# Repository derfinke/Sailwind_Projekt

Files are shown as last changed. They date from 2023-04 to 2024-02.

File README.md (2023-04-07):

# Projektarbeit: Sailwind Steuerung
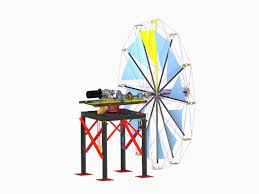
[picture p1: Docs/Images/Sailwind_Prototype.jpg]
Product Name Screen Shot
 \
Firmware/Schaltplan für die Steuerung des Sailwind 4.0 Projekts.\
[ Für weitere Informationen](https://www.sailwind-power.eu/)

## Geteilte Dokumente
[Bauteile Tabelle](https://drive.google.com/drive/folders/1qaNF0T8h1C8PEslQvWO4vngNG08Ppogr?usp=share_link)

## Roadmap
- [x] Erstellung des Schaltplans
- [ ] Erstellung des PCB Designs
	- [x] Auswahl der Bauteile
- [ ] Erstellung der Firmware
	- [x] Definieren der genutzen Ports
	- [ ] Definition des Ethernet Protokoll
	- [ ] Siehe [open issues](https://github.com/derfinke/Sailwind_Projekt/issues)

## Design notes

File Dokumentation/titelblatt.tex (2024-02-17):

\begin{titlepage}
\vspace*{-3cm}
    \begin{figure}[ht]
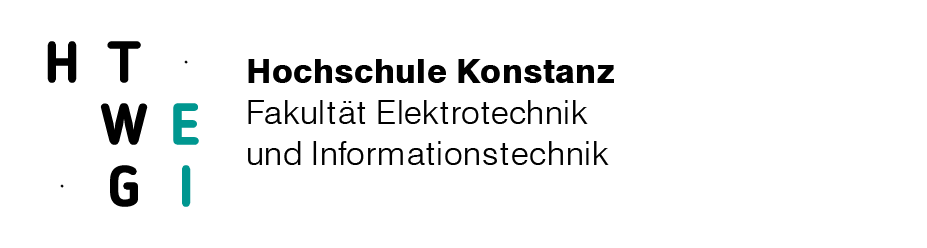
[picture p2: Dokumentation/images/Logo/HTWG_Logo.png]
        \hspace{7cm}\subfloat{{ }}
    \end{figure}
        
	\begin{center}
		\vspace*{1cm}
		\LARGE\bf\myTopic\\
		\vspace*{1cm}
		\normalsize\rm
		\vspace*{1cm}
		\textbf{Projektarbeit}\\
		\vspace*{0.5cm}
		An der Fakultät Elektro- und Informationstechnik \\
		\vspace*{0.5cm}
		vorgelegt von  \\
	    \vspace*{0.25cm}
		\textbf{\myAutorTwo\:und \myAutor}  \\
		\vspace*{0.25cm}
		Matrikelnummer: \myMatrikelnummerTwo\:und \myMatrikelnummer \\
		\vspace*{1cm}
		Hochschule Konstanz für Technik, Wirtschaft und Gestaltung \\
		\vspace*{1cm}
		Hochschulbetreuer: \\
		\textbf{\mySupervisorTwo}\\
		\textbf{\mySupervisor}\\
		\vspace*{1cm}
		\textbf{Konstanz den \today}
	\end{center}
\end{titlepage}
\newpage
\setcounter{page}{2}

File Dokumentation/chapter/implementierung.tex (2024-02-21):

\section{Software}
Die Steuerung der Segel soll durch zwei verteilte Systeme erfolgen, die über eine Ethernet-Verbindung miteinander kommunizieren. Die Idee dahinter ist, die Berechnungen für die Ausrichtung der Segel in Abhängigkeit der Windstärke und -Richtung (Controllino) von der hardwarenahen Verarbeitung der Sensoren und Aktuatoren (STM32) logisch zu trennen. \\

\noindent
Die vorliegende Arbeit konzentriert sich dabei lediglich auf das System der Sensoren und Aktuatoren, welches mit dem STM32 realisiert wurde. Die Aufgabe dieses Systems ist, zunächst die Linearführung zu kalibrieren, damit die aktuelle Position korrekt ermittelt werden kann. Außerdem soll über die Buttons am Gehäuse und zusätzlich über einen Webserver eine manuelle Steuerung ermöglicht werden. Während des Automatikbetriebs geschieht ein regelmäßiger Austausch aller relevanter Daten über eine REST basierte Schnittstelle. Dies beinhaltet u.A. die Information über aktuelle Windbedingung, Position der Segel, eventuelle Fehlerzustände (z.B. Motorfehler oder Überstrom) und daraus resultierende Befehle zur Anpassung der Segelstellung.
Für die Implementierung wurde die Software in komponentenorientierte Module eingeteilt:
\begin{figure}[H]
	\centering
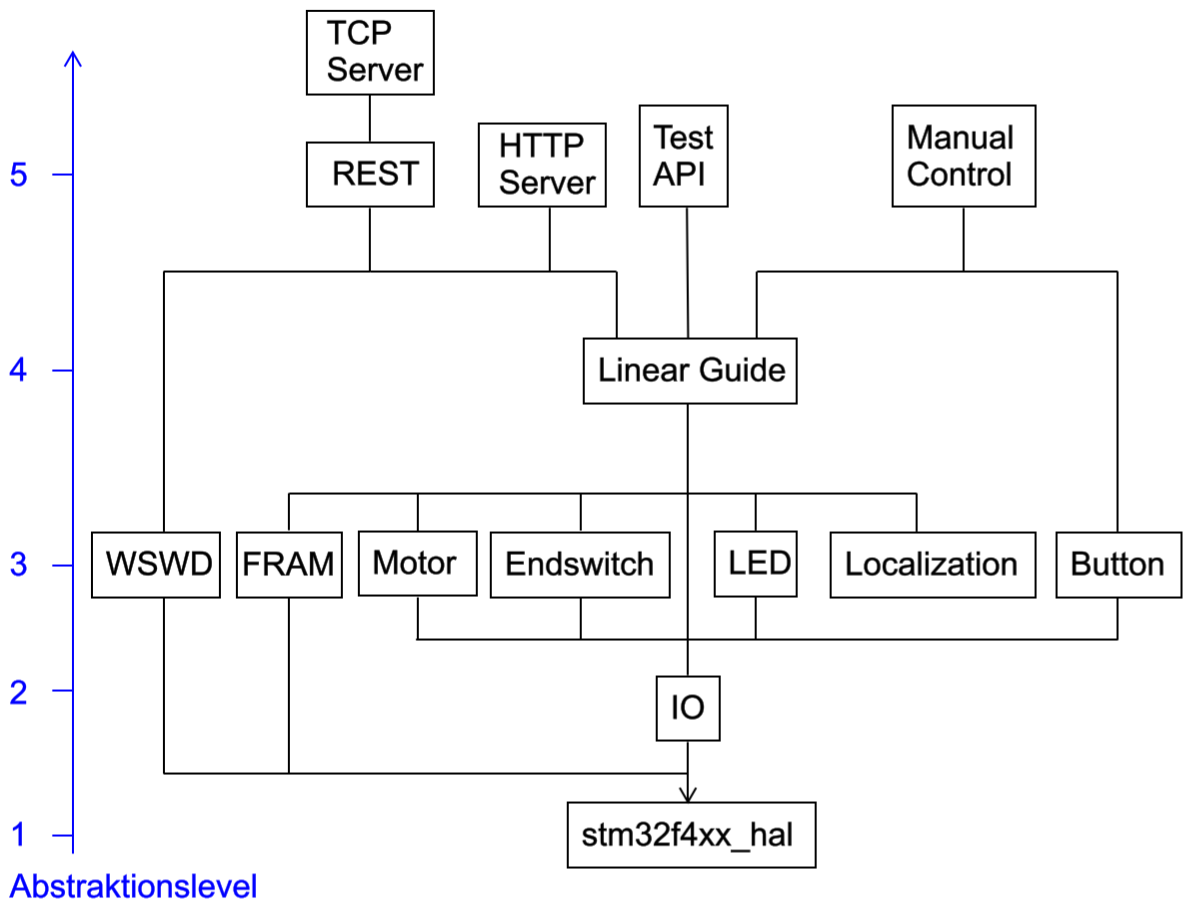
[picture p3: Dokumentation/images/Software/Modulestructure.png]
	
	\caption{Software Modulstruktur}
	\label{fig:modulestructure}
\end{figure}
\noindent
\autoref{fig:modulestructure} zeigt abwärtsgerichtet, wie die einzelnen Module aufeinander zugreifen. Auf unterster Abstraktionsebene laufen jegliche Operationen über die Standardbibliothek des Mikrocontrollers \verb|stm32f4xx\_hal|. Darüber liefert das \verb|IO|-Modul ein Set aus Hilfsfunktionen und -Strukturen für den allgemeinen Zugriff auf die \ac{GPIO}-Pins und zum Auslesen analoger Messwerte der einzelnen Sensoren.\\

\noindent
Ebene drei umfasst hauptsächlich Module, welche alle relevanten Funktionalitäten der physischen Teilkomponenten des Systems implementieren, wie z.B. das Anemometer \verb|WSWD| oder der \verb|Motor|. Einige davon greifen dabei auf das \verb|IO|-Modul zu, wobei der allgemeine GPIO-Zugriff von einer spezifischen Funktion eingekapselt wird, wie z.B. das Einschalten einer LED im Falle des \verb|LED|-Moduls. Eine Ausnahme ist das \verb|Localization|-Modul, welches keine physische Komponente darstellt, sondern einige Hilfsfunktionen zur Kalibrierung und Positionsberechnung bereitstellt.\\

\noindent
Während die Module bis Ebene drei überwiegend allgemeingültig entworfen sind, enthält das \verb|Linear Guide|-Modul anwendungsspezifische Funktionen. Als zentrales Element bildet dieses ein High-Level Interface zur Verwendung der Teilkomponenten \verb|FRAM|, \verb|Motor|, \verb|Endswitch|, \verb|LED|, \verb|Localization| und \verb|IO|. \\

\noindent
Die Module der obersten Abstraktionsebene bilden die direkten Schnittstellen zur Außenwelt. Das \verb|Manual Control|-Modul ermöglicht die manuelle Steuerung der Linearführung über die User-Buttons am Gehäuse und insbesondere die Umsetzung des Kalibrierungsprozesses. Auf der anderen Seite kann das System auch durch einen \ac{HTTP} Webserver überwacht und gesteuert werden. Außerdem werden im \verb|REST|-Modul die Anfragen des Controllinos über die \verb|TCP Server|-Verbindung verarbeitet, wie bereits oben erwähnt. Zuletzt wurde ein \verb|Test|-Modul implementiert, dass die Funktionalitäten der Module auf Ebene drei verifiziert. Dazu wurde ein einfaches Batch-Skript geschrieben, das die einzelnen Testcases auflistet und die Auswahl über UART an den  Mikrocontroller sendet, sodass im \verb|Test|-Modul eine entsprechende Funktion ausgeführt wird. In den nachfolgenden Abschnitten wird genauer auf einige Module eingegangen, beginnend mit dem untersten Abstraktionslevel.

\subsection{IO-Modul}
Dieses Modul soll den lesenden und schreibenden Zugriff auf jegliche GPIO-Pins erleichtern, die zur Kontrolle jeglicher Steuerelemente angeschlossen wurden. Allgemein besteht das System aus analogen und digitalen Sensoren bzw. Aktuatoren. Für jede Form wurde eine repräsentative Struktur definiert, in der alle relevanten Daten zusammengefasst werden.
\subsubsection{Digitale Pins}
Für digitale Ein- und Ausgänge wurde eine gemeinsame Struktur \verb|IO_digitalPin_t| definiert:
\begin{lstlisting}[language=C, caption={Struktur für digitale Pins}, label={lst:digitalPin}]
typedef struct {
	GPIO_TypeDef *GPIOx;
	uint16_t GPIO_Pin;
	GPIO_PinState state;
} IO_digitalPin_t;
\end{lstlisting}
Dabei ist der GPIO-Pin durch eine Nummer \verb|GPIO_Pin| und einen Port \verb|GPIOx| definiert. Zusätzlich wird in der Struktur der aktuelle Zustand \verb|state| (null oder eins) gespeichert. Diese kann nun einer Funktion als Pointer übergeben werden, um z.B. den neuen Zustand auszulesen:
\begin{lstlisting}[language=C, caption={Einlesen eines digitalen Pin-Zustands}, label={lst:digitalRead}]
GPIO_PinState IO_digitalRead(IO_digitalPin_t *dig_IN) {
	dig_IN->state = HAL_GPIO_ReadPin(
		dig_IN->GPIOx, dig_IN->GPIO_Pin
	);
	return dig_IN->state;
}
\end{lstlisting}
Dabei wird lediglich die Funktion \verb|HAL_GPIO_ReadPin()| der \verb|stm32f4xx_hal| Bibliothek aus \autoref{fig:modulestructure} aufgerufen, welche die zuvor besagten Attribute des Pins entgegennimmt und dessen Wert zurückgibt. Das Speichern dieses Werts in \verb|state| hat den Vorteil, dass damit auf eine Änderung des Zustandes geschlossen werden kann. Dies ist z.B. für das Erfassen der steigenden und fallenden Flanke während eines Knopfdrucks sinnvoll und wurde wie folgt realisiert:
\begin{lstlisting}[language=C, caption={Detektion einer Flanke}, label={lst:edgeDetection}]
boolean_t IO_digitalRead_state_changed(IO_digitalPin_t *dig_IN) {
	GPIO_PinState previous_state = dig_IN->state;
	GPIO_PinState current_state = IO_digitalRead(dig_IN);
	return current_state ^ previous_state;
}
\end{lstlisting}
Die Funktion in \autoref{lst:edgeDetection} gibt durch eine logische exklusiv-oder-Verknüpfung von letztem und aktuellem Zustand in Form eines booleschen Werts an, ob sich der Zustand geändert hat oder nicht. Äquivalent zu \autoref{lst:digitalRead} ist eine Funktion \verb|IO_digital_write()| implementiert, die den gewünschten Pegel an einem entsprechenden Ausgangspin schaltet.
\subsubsection{Analoge Pins}
Etwas komplexer wird es mit dem Auslesen von analogen Sensorwerten. Dazu wird ein ADC-Kanal (\verb|ACD_Channel|) des STM32 verwendet, der eine Spannung am Pin zwischen 0 und 3.3V in eine 12 bit Sequenz quantisiert und folglich als Integerwert \verb|ADC_val| zwischen 0 und 4096-1 zurückgibt. Idealerweise entspricht dieser Wertebereich umgewandelt dem des Sensors, jedoch ist dies durch Ungenauigkeiten in der Hardware nicht immer der Fall, weshalb dies durch zusätzliche Grenzwerte in der Struktur für analoge Sensoren berücksichtigt wird:
\begin{lstlisting}[language=C, caption={Struktur für analoge Sensoren}, label={lst:analogSensor}]
typedef struct {
	ADC_HandleTypeDef *hadc_ptr;
	IO_SensorType_t Sensor_type;
	uint32_t ADC_Channel;
	uint16_t ADC_val;
	uint16_t max_sens_val;
	uint16_t sens_val;
	uint16_t min_sens_val;
	float max_pin_volt;
	float min_pin_volt;
} IO_analogSensor_t;
\end{lstlisting}
Die Bezeichnung \verb|sense_val| aus \autoref{lst:analogSensor} steht dabei für den Wert in der Einheit des gewünschten Sensormesswerts und \verb|pin_volt| für den umgewandelten Spannungswert am Pin. Damit lässt sich der Sensormesswert wie folgt berechnen:\footnote{Funktion dient zur Veranschaulichung und wurde nicht exakt in dieser Form implementiert}
\begin{lstlisting}[language=C, caption={Konvertierung des rohen Analogwerts}, label={analogRead}]
void IO_Convert_from_ADC(IO_analogSensor_t *s) {
	float pin_volt = 3.3 * s->ADC_val / (4096-1)
	s->sens_val = (s->max_sens_val - s->min_sens_val) /
	              (s->max_pin_volt - s->min_pin_volt) *
	              (pin_volt        - s->min_pin_volt) +
	               s->min_sens_val
}
\end{lstlisting}
In umgekehrter Weise funktioniert die Umwandlung eines gewünschten Wertes in einen quantisierten Spannungswert für einen analogen Aktuator mithilfe einer entsprechenden Struktur \verb|IO_analogActuator_t|. \\

\noindent
Die Module \verb|LED|, \verb|Button| und \verb|Endswitch|, repräsentieren physische Komponenten, die jeweils durch einen einfachen digitalen Pin angesteuert werden und enthalten daher lediglich Wiederverwendungen der Funktionen \verb|IO_digitalWrite()|, um eine LED ein und auszuschalten, \verb|IO_digitalRead_state_changed()|, um einen Knopfdruck zu erfassen oder \verb|IO_digitalRead()|, um den Zustand eines Endschalters zu lesen. Dagegen wird der BG 45x30 SI Gleichstrommotor aufgrund seiner internen Regelung durch mehrere verschiedene Ein- und Ausgänge angesteuert.
\subsection{Motor-Modul}
Die Aufgabe des Motors ist, die Segelstellung entlang der Linearführung anzupassen. Dazu ermöglichen dessen digitale Eingänge gemäß \autoref{tab:digitale_Eingaenge} eine flexible Einstellung der Drehzahl und -Richtung. Alternativ zu den konfigurierbaren fixen Geschwindigkeiten 1 und 2 kann mit dem analogen Eingang auch eine beliebige Drehzahl dynamisch vorgeben werden. Damit konnte eine Drehzahlrampe realisiert werden, die einen sanfteren Brems- und Beschleunigungsvorgang gewährleistet.\\

\noindent
Über die digitalen Ausgänge kann der Ist-Zustand überwacht werden, darunter die aktuelle Drehrichtung und ob ein Fehler vorliegt. Zusätzlich kann durch ein Puls-Signal mit 12 Pulsen pro Umdrehung auf die Drehzahl geschlossen werden. Da der Motor in diesem Fall jedoch unter Drehzahlregelung betrieben wird, kann, sofern kein Fehlersignal vorliegt, von einer ausreichend präzisen Einhaltung der eingestellten Drehzahl ausgegangen werden. Dennoch ist das Puls-Signal von zentraler Bedeutung, da aufgrund der Gewindesteigung der Linearführung und der Anzahl der Pulse ausgehend von einem Endpunkt die aktuelle Position und somit die Segelstellung ermittelt werden kann. Das Zählen der Pulse geschieht jedoch der Thematik entsprechend in einer Funktion des \verb|Localization|-Moduls, die durch einen externen Interrupt am zuständigen GPIO-Pin von steigenden Flanken getriggert wird.\\

\noindent
Orientiert an der Architektur des \verb|IO|-Moduls dient auch hier eine Struktur als gemeinsamer Zugriffspunkt aller relevanter Daten des Motors:
\begin{lstlisting}[language=C, caption={Struktur des Motors}, label={lst:motor}]
typedef struct {
	Motor_function_t current_function;
	Motor_INs_t INs;
	IO_analogActuator_t AIN_set_rpm;
	IO_digitalPin_t OUT2_error;
	IO_digitalPin_t OUT3_rot_dir;
	uint16_t normal_rpm;
	uint16_t rpm_set_point;
	uint16_t ramp_final_rpm;
	uint32_t ramp_last_step_ms;
	boolean_t ramp_activated;
} Motor_t;
\end{lstlisting}
\subsubsection{Funktionsvorgabe}
Grundlage zur Steuerung des Motors ist die Implementation der Funktionsvorgabe über die digitalen Eingänge, die in der Struktur nach \autoref{lst:motor} durch ein Array \verb|INs| des Typs \verb|IO_digitalPin_t| organisiert sind. Zur einfachen Anwendung wurde ein enum \verb|Motor_function_t| definiert, der alle Funktionen entsprechend \autoref{tab:digitale_Eingaenge} bezeichnet und von oben beginnend von null bis sieben nummeriert. Durch eine geeignete Umrechnung in einen Binärwert zwischen 00 und 11 können aus den einzelnen Stellen direkt die passenden beiden Pins über das Array indiziert und mit den Stellenwerten beschrieben werden. Das nachfolgende Listing zeigt die genaue Umsetzung dieses Verfahrens.
\begin{lstlisting}[language=C, caption={Einstellung der Motorfunktionen}, label={lst:motorFunction}]
void Motor_set_function(Motor_t *motor, Motor_function_t func) {
	motor->current_function = func;
	uint8_t pin_offset = (func >= 4) * 2;
	int8_t function_bits = func - pin_offset * 2;
	for (int i = 0; i < 2; i++) {
		GPIO_PinState state = function_bits & 2 ? 1 : 0;
		uint8_t IN_idx = i + pin_offset;
		IO_digitalWrite(&motor->INs[IN_idx], state);
		function_bits <<= 1;
	}
}
\end{lstlisting}
Im ersten Schritt wird überprüft, ob die Eingänge 0 \& 1 oder 2 \& 3 für die Funktion zuständig ist. Letzteres ist der Fall, wenn der Funktionsindex in der oberen Hälfte (\verb|>=4|) liegt. Das Beschreiben der beiden Eingänge erfolgt iterativ über eine For-Schleife, wobei die Pins durch die Zählvariable \verb|i| indiziert werden. Falls die Eingänge 2 \& 3 zuständig sind, muss folglich ein \verb|pin_offset| von zwei auf den Index addiert werden. Ebenfalls wird dann die Funktionsnummer mit vier subtrahiert, damit aus dem resultierenden Wert in \verb|function_bits| der zweistellige Binärwert errechnet werden kann.
Durch die bitweise und-Verknüpfung mit zwei und einer anschließenden einfachen links-shift Operation (\acs{MSB}-first) werden die einzelnen Binärstellen der Reihe nach berechnet und mit \verb|IO_digitalWrite()| als neuen Zustand \verb|state| am passenden Pin geschaltet.
\subsubsection{Drehzahlrampe}
Darauf basierend wurden konkrete Funktionen zur Steuerung des Motors implementiert. Das Kernelement ist dabei die Realisierung der Drehzahlrampe innerhalb der Funktion \verb|Motor_speed_ramp()|, welche in der Hauptschleife des Programms durchgehend ausgeführt wird. Die Rampe kann dabei durch eine Funktion \verb|Motor_start_moving()| aktiviert werden, die mit \verb|Motor_set_function()| Links- oder Rechtslauf einstellt und anschließend das Flag \verb|ramp_activated| aus \autoref{lst:motor} setzt. Darauf hin wird der Drehzahlwert \verb|rpm_setpoint| in regelmäßigen Zeitschritten um einen konstanten Wert erhöht. Nach Konfiguration auf \textit{Drehzahlvorgabe} (\autoref{tab:digitale_Eingaenge}) kann die neue Soll-Drehzahl an dem analogen Eingang \verb|AIN_set_rpm| mit \verb|IO_analogWrite()| umgesetzt werden. Dies geschieht solange, bis die Zieldrehzahl \verb|ramp_final_rpm=normal_rpm| erreicht ist und die Rampe wieder deaktiviert wird. Ebenso kann die Rampe mit \verb|Motor_stop_moving()| für den Bremsvorgang aktiviert werden, wobei \verb|ramp_final_rpm=0| gesetzt wird und die Drehzahl in gleicher Weise schrittweise reduziert wird. Aufgrund einiger Tests wurde für die Rampe eine Schrittdauer von 13 ms und eine Schrittweite von 10 rpm mit einer Normaldrehzahl von 1600 rpm festgelegt, sodass sich folgender zeitlicher Verlauf ergibt:
\begin{figure}[H]
	\centering
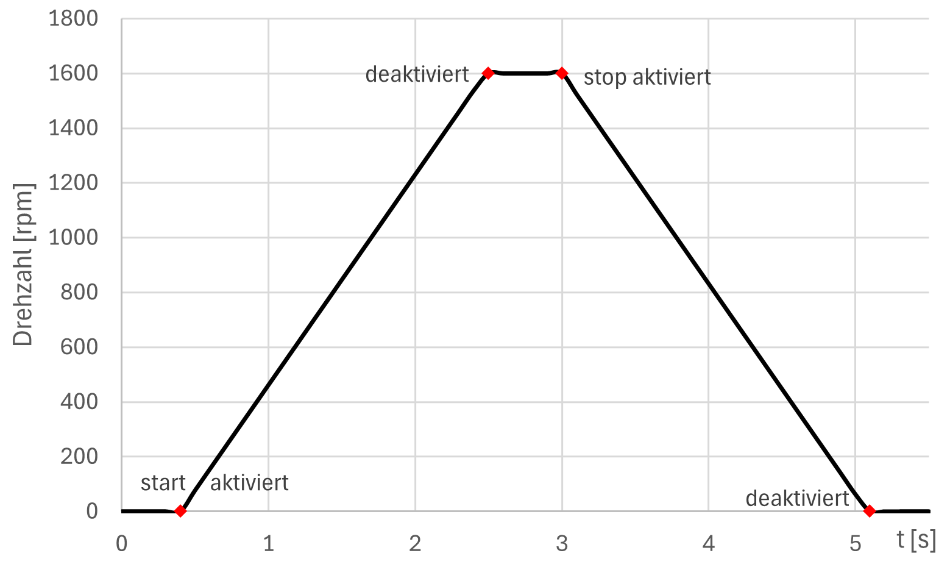
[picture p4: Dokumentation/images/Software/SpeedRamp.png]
	
	\caption{Drehzahlrampe: Beschleunigen und Bremsen}
	\label{fig:speedRamp}
\end{figure}
\noindent
Die Stopp-Funktion bietet zusätzlich die Möglichkeit über einen booleschen Parameter \verb|immediate| z.B. während einer Notabschaltung den Motor abrupt anzuhalten. In diesem Fall wird nicht die Rampe aktiviert sondern direkt die Motorfunktion \textit{Motor aus} gesetzt. 
\subsection{Steuerung der Linearführung}
Nachdem die allgemeine Steuerung des Motors implementiert ist, gilt es, diese auf die Positionierung der Segel über die Linearführung anzuwenden. 
\subsubsection{Kalibrierung}\label{subsubsec:Kalibrierung}
Damit später eine bestimmte Stellung angefahren werden kann, muss die aktuelle Position jederzeit bekannt sein. Wie bereits erwähnt, dient das Puls-Signal des Motors als Maß, wie weit sich die Position von einem Startpunkt entfernt hat. Jedoch muss dieser Punkt erst angefahren werden, was durch die Detektion der Endschalter keine Schwierigkeit darstellt. Damit kann die absolute Position anhand der Puls-Zahl und der Gewindesteigung ermittelt werden. Für die Einstellung der Segel wird vom Controllino eine Prozentzahl vorgegeben wie weit gerollt oder getrimmt werden soll. Um diesen Wert auf eine absolute Position auf der Linearführung abzubilden, muss zusätzlich die Distanz zwischen den beiden Endpunkten ermittelt werden. Außerdem soll die Grenze zwischen Roll- und Trimmbereich nachträglich manuell angepasst werden können, um potenzielle Asymmetrien in der Seilführung der Segel auszugleichen. Der gesamte Ablauf der Kalibrierung wurde in Form einer Zustandsmaschine realisiert, wie in \autoref{fig:calibration} dargestellt.
\begin{figure}[H]
	\centering
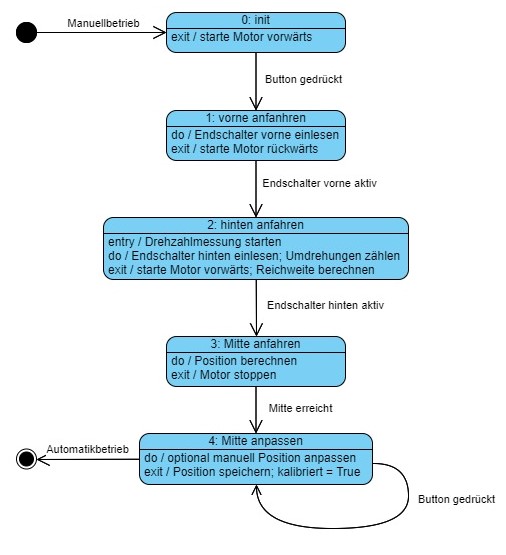
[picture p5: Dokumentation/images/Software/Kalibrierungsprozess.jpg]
	
	\caption{Kalibrierungsprozess}
	\label{fig:calibration}
\end{figure}
\noindent
Die Eintrittsbedingung der Kalibrierung ist das Einschalten des manuellen Betriebsmodus durch den Kippschalter am Gehäuse oder alternativ über den Webserver. Aus dem Ausgangszustand heraus muss der Knopf \textit{Speichern/Bestätigen} aus \autoref{fig:Bedienung} gedrückt werden, um die automatische Kalibrierung einzuleiten. Dies ist mit dem starten des Motors in Vorwärtsrichtung und dem Übergang in Zustand 1 verbunden. Anschließend wird der vordere Endschalter abgefragt, bis dieser aktiviert wird und die Endposition erreicht ist. Von dieser Position aus beginnt die Pulszählung, damit nach Ankunft am anderen Ende die zurückgelegte Distanz berechnet werden kann. Aus dieser Distanz wird daraufhin die Mitte bestimmt und angefahren. Ist diese erreicht, kann zuletzt die tatsächliche Grenze manuell über die Knöpfe \textit{Trimmen} und \textit{Rollen} angefahren und mit dem erneuten Druck des einleitenden Knopfes bestätigt werden. Als Feedback blinkt dabei die LED \textit{Position gespeichert}. Ebenso aktivieren bzw. deaktivieren sich nun nach der Einteilung der Bereiche je nach Positionierung die entsprechenden LEDs (\textit{Im Trimmungsbereich} / \textit{Im Rollbereich}).\\

\noindent
Da die Grenze in Zustand 4 mit dem entsprechenden Knopf beliebig oft angepasst werden kann, ist es durch das selbe Signal nicht möglich, den kompletten Prozess von vorne zu starten, ohne das System neuzustarten. Daher wurde ein Timer mit einem periodischen Callback konfiguriert, der die Dauer des Knopfdrucks ermittelt und ab einer Druckdauer von 3s die Zustandsmaschine zurücksetzt, anstatt lediglich die Grenze zu überschreiben. Nach Abschluss der Kalibrierung kann in den Automatikbetrieb gewechselt werden. Im Automatikbetrieb kann der Controllino aufgrund der bereitgestellten Daten regelmäßig die optimale Segelstellung neu berechnen und an den STM32 zurückgeben. Der nächste Abschnitt beschäftigt sich damit, wie genau die gewünschte Segelstellung in eine Position auf der Linearführung umgerechnet wird. 
\subsubsection{Umsetzung einer Rollung/Trimmung}
Der Befehl einer Segelanpassung wird vom Controllino durch einen Modus (Rollen oder Trimmen) und eine Prozentzahl definiert. \autoref{fig:linearGuide} zeigt graphisch die Bedeutung dieser Angabe bezüglich der Positionierung an der Linearführung.
\begin{figure}[H]
	\centering
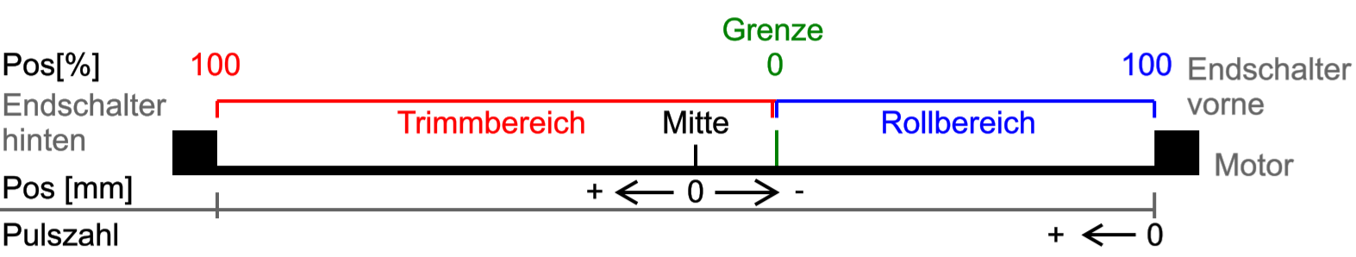
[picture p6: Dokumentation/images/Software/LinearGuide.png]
	
	\caption{Rollung und Trimmung an der Linearführung}
	\label{fig:linearGuide}
\end{figure}
\noindent
In diesem Beispiel weicht die Grenze zwischen den beiden Bereichen stark von der tatsächlichen Mitte ab, um die Möglichkeit der manuellen Anpassung, zu verdeutlichen. Zur besseren Lesbarkeit der aktuellen Position wird diese in einem Zwischenschritt in mm umgerechnet und die Mitte der Gesamtdistanz auf null zentriert. In dieser Einheit werden jegliche Positionsberechnungen durchgeführt. \\

\noindent
Für die Umwandlungen zwischen Prozent, mm und Pulsen werden alle relevanten Daten in einer gleichnamigen Struktur des \verb|Localization|-Moduls festgehalten. \autoref{lst:sailAdjustment} zeigt die Ermittlung der gewünschten Position in mm mithilfe dieser Struktur aufgrund eines Segelanpassungsbefehls:
\begin{lstlisting}[language=C, caption={Berechnung der Zielposition}, label={lst:sailAdjustment}]
void Linear_Guide_set_desired_roll_trim_percentage(
	Localization_t *loc, uint8_t percentage, 
	adjustment_mode_t mode
)
{
	int8_t sign = mode == adjustment_mode_roll ? 1 : -1;
	int32_t roll_trim_distance = loc->end_pos_mm
	                           + sign * loc->center_pos_mm;
	loc->desired_pos_mm = (int32_t) 
	(- sign * (roll_trim_distance * (percentage / 100.0F)
	           - sign * loc->center_pos_mm));
}
\end{lstlisting}
Zunächst wird ein Vorzeichen \verb|sign| festgelegt, da der Rollbereich im negativen und der Trimmbereich im positiven mm Bereich liegt. Je nachdem welche Modus gewünscht ist, berechnet sich dessen Streckenanteil an der Linearführung aus der Distanz \verb|end_pos_mm| von der Mitte bis zu einem Endpunkt und dem Abstand \verb|center_pos_mm * sign| von der Mitte bis zur gewählten Grenze \verb|center_pos_mm|. Von dieser Strecke wird der gewünschte Anteil \verb|percentage| durch das Vorzeichen auf die richtige Seite orientiert. Zuletzt muss das addieren des Abstandes \verb|center_pos_mm * sign| wieder rückgängig gemacht werden.\\

\noindent
Nachdem die gewünschte Position in mm vorliegt, muss diese angefahren werden. Dazu muss diese mit der aktuellen Position der Linearführung verglichen werden, welche sich nach der Kalibrierung aus der Pulszahl des Motors ergibt. Die Pulszahl wird wie bereits erwähnt durch den externen Interrupt am zuständigen GPIO-Pin regelmäßig aktualisiert und in der Struktur \verb|Localization_t| aus \autoref{lst:sailAdjustment} festgehalten. Die Positionsumrechnung ist in einer Funktion des \verb|Localization|-Moduls implementiert, wie nachfolgend gezeigt:
\begin{lstlisting}[language=C, caption={Positionsberechnung aus dem Pulssignal des Motors}, label={lst:pulseToPos}]
void Localization_update_position(Localization_t *loc)
{
	uint16_t abs_pos = loc->pulse_count
	                 * loc->distance_per_pulse;
	loc->current_pos_mm = abs_pos - loc->end_pos_mm;
}
\end{lstlisting}
Dabei berechnet sich die zurückgelegte Strecke pro Puls \verb|distance_per_pulse| aus dem Quotienten der Gewindesteigung von 1.12 mm pro Umdrehung und der Pulsfrequenz des Motors von 12 Pulsen pro Umdrehung zu 0.093 mm pro Puls.
\subsubsection{Optimierung der Bewegungsübergänge}
Die Steuerung der Linearführung wird durch das Aktivieren von Drehzahlrampen gelöst, um sanfte Beschleunigungs- und Bremsvorgänge zu ermöglichen. Allerdings gibt es unter dem bisherigen Stand der Implementierung mehrere Situationen, in denen es trotzdem noch zu abrupten Bewegungsänderungen kommt. Eine davon stellt das Erreichen eines Endpunktes dar, denn die Aktivierung des Endschalters ist direkt mit einem hardware-geregelten Stopp des Motors verbunden. Ebenfalls kann die Rampenfunktion nicht zwischen Beschleunigung in Vorwärts- und Rückwärtsrichtung unterscheiden, weshalb bei ein Befehl in die umgekehrte Richtung sofort umgesetzt wird. Ein anderes vielleicht noch wichtigeres Problem ist, dass eine gewünschte Position nicht korrekt angefahren werden kann, da der Motor nach dem Stopp-Befehl aufgrund der Rampe noch ein kleines Stück weiterfährt.\\

\noindent
Die Lösung dieser Probleme liegt in der Ermittlung des Bremsweges sowie der Einführung einer Warteschlange für Zielpositionen. Darauf basierend wurde ein Algorithmus zur optimierten Koordination der Steuerbefehle implementiert, wie nachfolgend in Form eines Programmablaufplans dargestellt:
\begin{figure}[H]
	\centering
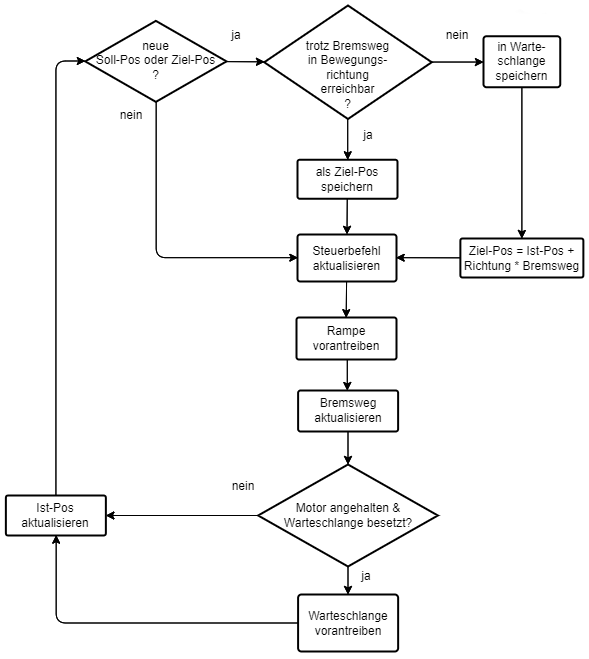
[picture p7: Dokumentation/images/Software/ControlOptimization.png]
	
	\caption{Optimierung der Steuerbefehle}
	\label{fig:controlOptimization}
\end{figure}
\noindent
Eine Soll-Position kann entweder durch die manuelle Steuerung oder durch eine gewünschte Segelstellung vom Controllino während des Automatikbetriebs vorgegeben werden. Hat sich diese geändert, kann es sein, dass sich die Linearführung wegen eines vorhergegangenen Befehls bereits in Bewegung befindet. In diesem Fall muss überprüft werden, ob sich die Soll-Position in Bewegungsrichtung vor der aktuellen Position befindet und ggfs. ob der Abstand aufgrund des Bremsweges noch erreichbar ist. Wenn diese Bedingungen nicht erfüllt sind, wird die Soll-Position nicht direkt als neues Ziel gesetzt sondern in einer Warteschlange gespeichert, wobei diese eigentlich nur eine einzelne Variable der \verb|Localization_t| Struktur ist. Damit die neue Soll-Position trotzdem so schnell wie möglich erreicht wird, bildet der in Fahrtrichtung nächste noch erreichbare Punkt die neue Zielposition. Danach kann der Steuerbefehl aktualisiert werden (Vorwärts, Rückwärts oder anhalten). Nach Vorantreiben der Rampe muss der Bremsweg aufgrund der aktuellen Drehzahl ebenfalls neu berechnet werden. Ist der Motor zum Stillstand gekommen, kann sofern vorliegend die Position aus der Warteschlange als neues Ziel vorgerückt werden. Zuletzt muss natürlich auch die aktuelle Position der Linearführung aktualisiert werden bevor der Kreislauf von neuem beginnt. \\

\noindent
Sollte eine Soll-Position auch nach einem Richtungswechsel aufgrund einer Fehlberechnung des Bremsweges verfehlt werden, wird diese einfach erneut in die Warteschlange gesetzt, sodass sich die exakte Position garantiert einpendelt. Zusammenfassend werden nun mithilfe der Ziel-Warteschlange abrupte Richtungswechsel vermieden und durch die Berechnung des Bremsweges kann das System rechtzeitig anhalten, um die Soll-Position präzise anzufahren oder den Aufprall am Endschalter zu verhindern.
\subsubsection{Wiederherstellung der Position}
Die in Kapitel \ref{subsubsec:Kalibrierung} beschriebene Kalibrierung ist ein zeitintensiver Prozess. Damit diese nicht bei jedem Programmneustart erneut durchgeführt werden muss, wurde ein FRAM Speicher in der Hardware verbaut, um dort alle relevanten Informationen zur Wiederherstellung der aktuellen Position hineinzuschreiben und bei Bedarf wieder auszulesen. Für diese beiden Funktionen wurde ein Benutzerinterface im \verb|FRAM|-Modul implementiert.\\

\noindent
Das \ac{FRAM} Modul steuert den \ac{FRAM} über \ac{SPI} an. Der FRAM kann dabei über sechs Befehle gesteuert werden. Dabei wurden die Befehle: WREN(0000 0110b), RDSR(0000 0101b), READ(0000 0011b) und WRITE(0000 0010b) genutzt. Um auf den Speicher zu schreiben wird das \ac{WREN} Bit gesetzt. Hierfür wird der gleichnamige Befehl genutzt. Um zu überprüfen ob das Bit gesetzt wurde, wird es mit dem Befehl RDSR ausgelesen. Um den Speicher zu beschreiben wird mit dem WRITE Befehl gefolgt von einer 12Bit Addresse der Speicherbereich ausgewählt. Die darauffolgenden Bits werden in den Speicher geschrieben. Beim Auslesen mit dem Befehl READ ist das vorgehen gleich, nur werden hier keine zusätzlichen Bits übertragen. In der Software wurden dabei die zwei Funktionen \verb|FRAM_write| und \verb|FRAM_read| erstellt die für einen High Level Access sorgen. Über diese kann ein Puffer in den \ac{FRAM} geschrieben werden oder die Daten ausgelesen werden. Die Serialisierung und Deserialisierung, sowie das setzen des \ac{WREN} Bits wird beim Aufruf übernommen. Selbes gilt für das Auswählen des Chips über die Chip Select Leitung. Der Serial Clock Takt und die Übertragung von Daten geschieht mit dem \verb|HAL_SPI_Transmit|/\verb|HAL_SPI_Receive| Funktionen.\\

\noindent
Damit die Daten beim Auslesen zur Initialisierung des Systems aktuell sind, werden diese bei jeder Positionsänderung an der entsprechenden Speicheraddresse überschrieben. Die für die Lokalisierung nötigen Informationen werden zur Serialisierung innerhalb einer separaten Struktur organisiert, wie nachfolgend gezeigt:
\begin{lstlisting}[language=C, caption={Speicherformat der Positionsdaten}, label={lst:locSafeData}]
typedef struct {
	Loc_state_t state;
	int16_t pulse_count;
	uint16_t end_pos_mm;
	int16_t center_pos_mm;
	uint16_t start_pos_abs_mm;
} Loc_safe_data_t;
\end{lstlisting}
Die bisher nicht eingeführte Variable \verb|start_pos_abs_mm| entspricht dem vom Distanzsensor gemessenen Abstand der Position bei Aktivierung des vorderen, motor-seitigen Endschalters. Daraus lässt sich die mit dem Puls-Signal ermittelte Position mit dem Messwert des Sensors vergleichen. Die Bedeutung der Messung wird in Kapitel \ref{subsubsec:Fehlerbehandlung} genauer behandelt. \\

\noindent
Der Schreibprozess dieser Daten in das FRAM ist durch eine Funktion \\\verb|Linear_Guide_safe_Localization()| gegeben. \autoref{lst:safeLocalization} zeigt deren Implementierung.
\begin{lstlisting}[language=C, caption={FRAM Speichervorgang}, label={lst:safeLocalization}]
int8_t Linear_Guide_safe_Localization(Localization_t loc)
{
	uint8_t FRAM_buffer[sizeof(Loc_safe_data_t)];
	Localization_serialize(loc, FRAM_buffer);
	if(FRAM_write(FRAM_buffer, 
	              LINEAR_GUIDE_INFOS, 
	              sizeof(Loc_safe_data_t)) != HAL_OK)
	{
		printf("Saving Position failed!\r\n");
		return LG_LOCALIZATION_FAILED;
	}
	return LG_LOCALIZATION_SAFED;
}
\end{lstlisting}
Zunächst wird ein FRAM-Puffer der Größe des Speicherformats aus \autoref{lst:locSafeData} deklariert. Dann werden die entsprechenden Daten in der Funktion\\ \verb|Localization_serialize()| von der Struktur \verb|loc| in das richtige Format extrahiert und anschließend an den Puffer adressiert. Zuletzt werden die Daten innerhalb des Puffers durch \verb|FRAM_write()| an die definierte Addresse\\ \verb|LINEAR_GUIDE_INFOS| des physischen Speichers transferiert.\\

\noindent
Nachdem die Daten während des Betriebs kontinuierlich im FRAM aktualisiert werden, können diese bei einem Neustart des Systems in umgekehrter Weise wie in \autoref{lst:safeLocalization} durch \verb|FRAM_read()| abgerufen werden. \autoref{lst:deserialize} zeigt die Verarbeitung des resultierenden Ausgangspuffers \verb|buffer|:
\begin{lstlisting}[language=C, caption={Auslesen der Positionsdaten aus dem FRAM-Puffer}, label={lst:deserialize}]
static int8_t Localization_deserialize(
	Localization_t *loc, 
	uint8_t buffer[sizeof(Loc_safe_data_t)]
)
{
	Loc_safe_data_t *data = (Loc_safe_data_t *)
		malloc(sizeof(Loc_safe_data_t));
	memcpy(data, buffer, sizeof(Loc_safe_data_t));
	loc->state = data->state;
	loc->pulse_count = data->pulse_count;
	loc->end_pos_mm = data->end_pos_mm;
	loc->center_pos_mm = data->center_pos_mm;
	loc->start_pos_abs_mm = data->start_pos_abs_mm;
	free(safe_data_ptr);
	if (loc->state != Loc_state_5_center_pos_set)
	{
		return LOC_RECOVERY_RESET;
	}
	return LOC_RECOVERY_COMPLETE;
}
\end{lstlisting}
Im ersten Schritt wird ein Pointer \verb|data| im Speicherformat \verb|Loc_safe_data_t| entsprechend allokiert, damit diesem anschließend mit der C-Standard-Funktion \verb|memcpy()| die Daten aus dem Puffer übertragen werden können. Danach werden die einzelnen Werte der Reihe nach der Hauptstruktur des \verb|Localization|-Moduls übergeben. Zuletzt wird mit der \verb|state|-Variable überprüft, ob die Kalibrierung beim letzten Betrieb abgeschlossen wurde. Falls nicht, muss diese wiederholt werden, was das Rückgabe-Flag \verb|LOC_RECOVERY_RESET| signalisiert. War die Wiederherstellung der Lokalisierung erfolgreich, kann die aktuelle Position wie gehabt entsprechend \autoref{lst:pulseToPos} mit den Werten \verb|pulse_count| und \verb|end_pos_mm| ermittelt werden. Durch das Speichern der Grenze \verb|center_pos_mm| bleiben außerdem auch die zuvor eingestellten Trimm- und Rollbereiche erhalten.
\subsubsection{Fehlerbehandlung}\label{subsubsec:Fehlerbehandlung}
Mithilfe der Sensoren und dem Fehlersignal des Motors können verschiedene Fehlerzustände identifiziert werden. \autoref{tab:Fehlerbehandlung} listet diese auf, stellt deren Bedingung dar und wie damit umgegangen wird.
\begin{table}[H]
	\centering
	\begin{tabular}{|c|c|c|c|}
		                                                                                    \hline
		\textbf{ID} & \textbf{Bezeichnung} & \textbf{Bedingung}  & \textbf{Behandlung}   \\ \hline
		0           & Normal               & kein Fehler         & keine                 \\
		            &                      & identifiziert       &                       \\ \hline
		1           & Distanzfehler        & Toleranz von 1 cm   & Anpassung an Messwert \\
		            &                      & zwischen Messwert   &                       \\
		            &                      & und Pulsberechnung  &                       \\
		            &                      & überschritten       &                       \\ \hline
		2           & Windfehler           & max. Geschwindigkeit& Segel 100 \% einrollen\\
		            &                      & überschritten       &                       \\ \hline
		3           & Motorfehler          & Fehlersignal aktiv  & Notabschaltung        \\ \hline
		4           & Stromfehler          & Stromsensorwert von & Notabschaltung        \\
		            &                      & 4 A überschritten   &                       \\ \hline
	\end{tabular}%
	\caption{Fehlerzustände}
	\label{tab:Fehlerbehandlung}
\end{table}
\noindent
Bei jedem Fehler leuchtet als Feedback die LED \textit{Störung} aus \autoref{fig:Bedienung} auf. Während Fehler 1 vom System automatisch korrigiert werden kann, wird bei den anderen im Gegensatz dazu der weitere Betrieb solange blockiert, bis diese behoben sind. Die Toleranz zur maximalen Windgeschwindigkeit soll dabei vom Controllino festgelegt werden, da dort auch die Berechnungen zur optimalen Segelstellung durchgeführt werden. Daher wird der Windfehler auch nicht vom STM32 selbst gesetzt, sondern vom Controllino über das REST-Protokoll kommuniziert.
\subsection{Windmessung mit dem Anemometer}
Wie bereits in \autoref{Mangelnde_Präzision} aufgezeigt war die Präzision der Analogen Signale zwar ausreichend aber teilweise sehr ungenau. Aus diesem Grund wurde stattdessen die digitale RS485 Schnittstelle zur Übertragung der Windgeschwindigkeit und Windrichtung genutzt. Der WSWD bietet dabei mehrere Protokolle an, um diese Daten Formattiert zu übertragen. Dabei wurde das \ac{NMEA} Telegramm ausgewählt. Die Formatierung ist in \autoref{fig:NMEA_Protokoll} dargestellt.
\begin{figure}[H]
	\centering
	
	\caption{Aufbau eines NMEA Telegramm (vgl.\cite{WSWD}, S.61)}
	\label{fig:NMEA_Protokoll}
\end{figure}
\noindent Hier wird neben den Daten ($<WR>$ und $<WG>$) ebenfalls die Gültigkeit der Messung ($<V>$) und die Einheit der Geschwindigkeit ($<U>$) übertragen. Das versenden von Befehlen geschieht dabei aber in einem von MESA selbsterstellten Format:
\begin{table}[H]
	\centering
	\begin{tabular}{|l|l|l|l|}
		\hline
		\textbf{\textless{}ID\textgreater{}} & \textbf{\textless{}CM\textgreater{}} & \textbf{\textless{}PARAM\textgreater{}} & \textbf{\textless{}CR\textgreater{}\textless{}LF\textgreater{}} \\ \hline
		Geräte ID                            & Kommando                             & Parameter                               & Befehlsabschluss                                                \\ \hline
	\end{tabular}
	\caption{Aufbau eines Kommandos zur Einstellung des WSWD (vgl. \cite{WSWD}, S.26f.)}
	\label{tab:my-table}
\end{table}
\noindent Dieses wird im Normal Betrieb nicht benötigt, aber kann zur einmaligen Konfiguration des Sensors genutzt werden. Zur Konfiguration des Anemometers wurde z.B dabei der Befehl 42 angwewandt um die bereits Erklärten \ac{NMEA} Telegramme in einem regelmäßigen Abstand gesendet zu bekommen.\\

\noindent Die Befehle an das Anemometer werden über \ac{UART} Gesendet und Empfangen. Das Signal wird dann vom MAX3485 zu RS485 konvertiert. Da RS485 nur eine Halbduplex Kommunikation zulässt muss vorher über das Setzen eines Pins immer zwischen Senden und Empfangen gewechselt werden. Dies wurde in zwei Funktionen: \verb|WSWD_enable_receive| und \verb|WSWD_enable_send| realisiert. Diese prüfen zuerst den Status des Pins und ändern diesen falls nötig. Diese werden in den Sende und Empfangs Funktionen genutzt. Diese Serialisieren/Deserialisieren eine Zeichenkette mit einem Cast zu \verb|uint8_t*| und Versenden/Empfangen diese über die \verb|HAL_UART_Transmit|/\verb|HAL_UART_Receive| Funktionen:
\begin{lstlisting}[language=C, caption={Empfangen einer Nachricht vom WSWD}, label={lst:WSWDreceive}]
uint8_t WSWD_receive
(char* receive_buffer, uint8_t size_of_receive_buffer)
{
	WSWD_enable_receive();
	if(HAL_UART_Receive(&huart2, (uint8_t*)receive_buffer, 
	size_of_receive_buffer, WSWD_UART_TIMEOUT) != HAL_OK)
	{
		printf("error sending to WSWD\r\n");
	}
	return HAL_OK;
}
\end{lstlisting}
Beim Empfangen der Daten wird das komplette Telegramm als ein String gespeichert. Die Telegramm Struktur wird danach durch String Manipulation geprüft und die gesendeten Daten über die \verb|atof| Funktion zu einem nutzbaren \verb|float| Datentyp Konvertiert. Dasselbe Prinzip wird auch beim Versenden eines Befehles angewandt, nur das hier der String mit \verb|snprintf| zusammengesetzt wird.\\
\subsection{\ac{REST} Interface}
Das \ac{REST} Interface wird genutzt um mit dem Controllion zu kommunizieren. Zuerst wurden die hierfür benötigten \ac{HTTP} Befehle festgelegt. Da der Controllino als Client agieren soll und somit immer der Initiator der Kommunikation ist wurden die Befehle: \verb|GET| und \verb|PUT| als ausreichend angesehen. Die dabei mitversendeten Daten sollen im \ac{JSON} Format versendet werden. Die \verb|URL| auf die der Controllino über die \ac{API} zugreift wurden ebenfalls festgelegt. Diese wurden nach den unterschiedlichen Sensor- und Informationsdaten organisiert. Um z.B alle Informationen abzufragen sendet der Controllino den Befehl: \verb|GET /data|. Sollte er speziellere Infos abfragen wollen, wie z.B die Segelposition, sendet er den Befehl: \verb|GET /data/adjustment|. Eine Übersicht aller validen \ac{URL}s und JSON Formatierungen ist in \autoref{sec:REST} zu finden. Ein Beispiel für ein Antwort Paket für den \verb|GET /data/adjustment| Befehl ist in \autoref{lst:JSONantwort} zu sehen.
\begin{lstlisting}[language=C, caption={GET /data/adjustment Antwort Paket}, label={lst:JSONantwort}]
{
	"sail_pos": <(int) pitch/roll [+/- 0...100 %]>
}

\end{lstlisting}
Über den \verb|PUT| Befehl kann der Controllino einen Fehler setzen, eine gewünschte Position anfahren oder den Betriebsmodus der Steurung ändern. Zusätzlich kann auch der maximale Distanz Fehler und die maximale Drehzahl des Motors festgelegt werden. Der TCP-Server für die REST Kommunikation ist über den Port 2375 erreichbar und die Standard IP-Adresse als 192.168.0.123 definiert.\\

\noindent Zur Netzwerkkommunikation wurde der \ac{LWIP} Stack genutzt. Dieser beinhaltet allerdings keine bereits integrierte \ac{REST} \ac{API}. Aus diesem Grund wurde diese selbst implementiert. Dabei wurde ein \ac{TCP} Server erstellt. Dieser wird auf dem Mikrocntroller gehostet. Dieser nimmt die Rohdaten aus den Empfangen Paketen und speichert diese in einem Buffer. Der Buffer wird daraufhin an die \ac{REST} \ac{API} weitergegeben. Diese unterscheidet dabei zwischen den zwei möglich Befehlen und den akzeptierten \ac{URL}s. Falls diese nicht stimmen wird mit dem \ac{HTTP} Error code \verb|404 Not Found| geantwortet. Falls es sich um einen \verb|PUT| Befehl handelt, wird der mitgesendete JSON Payload auf eine Korrekte Formattierung geprüft. Hierfür wurde die cJson Bibliothek genutzt. Je nachdem ob die Formattierung stimmt wird mit \verb|200 OK| oder mit \verb|501 Not Implemented| bzw. \verb|400 Bad Request| geantwortet.\\
\noindent Beim versenden einer Antwort auf eine \verb|GET| Request wird ebenfalls mit Hilfe der cJson Bibliothek ein Payload zusammengebaut, der die aktuellen angeforderten Werte beinhaltet.
\subsection{Weboberfläche}
Der Webserver stellt eine alternative zu der physikalischen Bedienungsoberfläche dar. Diese ist in manchen Fällen ggü. der Bedienungsoberfläche zu bevorzugen, da hier schneller Anpassungen durchgeführt werden können und genauere Informationen dargstellt werden können.
\subsubsection{Funktionalität}
Die Weboberfläche, soll es einer Arbeitskraft erlauben den aktuellen Status, sowie Einstellungen des Gerätes abzufragen oder festzulegen. Dabei sollen dieselben Informationen, die der Controllino über die \ac{REST} \ac{API} abfragen kann auch auf diesem dargestellt werden. Zusätzlich dazu soll es hier auch möglich sein, dieselbe Funktionalität wie die Benutzeroberfläche zu bieten. Also sollte es möglich sein Manuell über die Weboberfläche die Segel zu Rollen und zu Trimmen. Dazu gehört auch die Auslösung einer Kalibrierungsfahrt.
Die Netzwerkeinstellungen sollten ebenfalls über die Weboberfläche gesetzt werden können. Dazu zählen die Aktivierung von DHCP, das Festlegen einer IP-Adresse und das Zurücksetzen dieser.
\subsubsection{Webseiten}
Die Webseiten wurden dabei nach ihrem Inhalt sortiert. Es wurden insgesamt sechs Seiten implementiert:
\begin{itemize}
	\item Index Seite
	\item Positionsdaten Seite
	\item Sensordaten Seite
	\item Einstellungs Seite
	\item Error Seite
	\item Login Seite
\end{itemize}
Als Beispiel ist die Index Seite in \autoref{fig:HTMLindex} dargestellt.
\begin{figure}[H]
	\centering
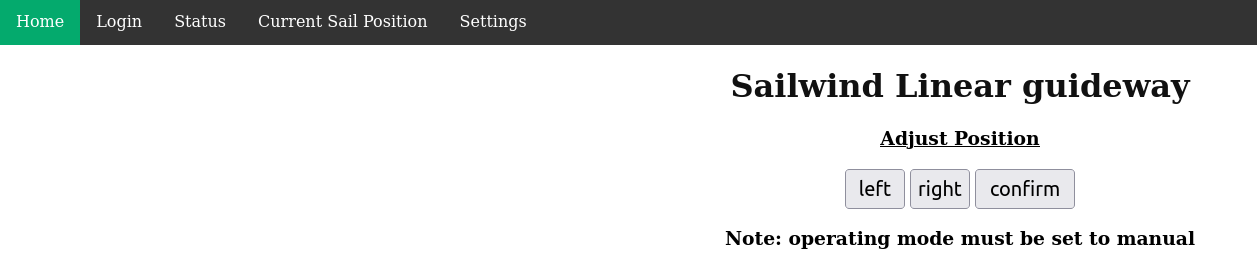
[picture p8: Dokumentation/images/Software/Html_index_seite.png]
	
	\caption{Index Seite des Webservers}
	\label{fig:HTMLindex}
\end{figure}
\noindent Hier befindet sich die manuelle Steuerung zur Positionierung der Segel. Auf allen Seiten wird dabei am oberen Rand eine Navigations Bar angezeigt mit der zu den anderen Seiten Navigiert wird. Auf der Positionsdaten Seite ist der aktuelle Betriebsmodus und die Trimmung/Rollung der Segel zu finden. Die Sensordaten Seite zeigt alle aktuellen Werte der Sensoren an und wird regelmäßig aktualisiert. Die Einstellungsseite zeigt die aktuellen Einstellungen und macht es möglich den Betriebsmodus zu ändern, das Gerät neuzustarten und eine neue IP Adresse festzulegen oder \ac{DHCP} zu aktivieren. Die Login Seite hat aktuell keine Funktion und dient nur als Platzhalter. Hier könnten später je nach Nutzer die aufrufbaren Webseiten eingeschränkt werden. So kann z.B ein Service Mitarbeiter auf alle Einstellungen zugreifen, während ein normaler Nutzer nur z.B die Sensordaten abfragen kann. Die Error Seite wird nur bei einer Zeitüberschreitung der Anfrage angzeigt und hat keinen weiteren Nutzen.
\subsubsection{Umsetzung}
Die Webserver erhält dieselbe \ac{IP} Adresse wie die \ac{REST} \ac{API} ist aber auf dem Port 80 erreichbar. Im Gegensatz zum \ac{REST} interface bietet \ac{LWIP} hier bereits schon eine fertige Webserver implementierung. Dabei können Daten über die \ac{SSI} und \ac{CGI} Handler Übertragen werden. Beim Aufrufen einer Webseite werden die im \ac{HTML} Code festgelegten \ac{SSI} Tags mit den entsprechenden Sensor Daten oder Text mit einer Rückmeldung für den User ersetzt. Hierfür wurde ein zentrales \verb|switch-case| festgelegt, das nach der Nummer des \ac{SSI} Tags unterscheidet und den dementsprechend String einfügt. Der \ac{CGI} Handler wird für Textboxen oder für Buttons genutzt. Für Buttons wurden dafür \ac{HTML} Forms genutzt. Diese haben als \verb|Action| einen \ac{URI} wie in \autoref{lst:URI} zusehen ist. 
\begin{lstlisting}[language=C, caption={GET /data/adjustment Antwort Paket}, label={lst:URI}]
	<form action="/form_control.cgi">
	<p>
	<input type="submit" 
	id="move" 
	value="confirm" 
	name="move" 
	style="width:100px;height:40px;font-size:20px;">
	</p>
	</form>
\end{lstlisting}
Wird jetzt z.B auf der Index Seite der Button \glqq{}Confirm\grqq{} angeklickt wird der String: \verb|/form_control.cgi?move=confirm| zum Mikrocontroller gesendet. Auf Basis dieses String kann daraufhin eine Aktion gewählt werden und z.B die Anzeige auf dem Webserver verändert werden. Textinputs funktionieren ähnlich nur das sie den Inhalt der Textbox nach der \ac{URI} beinhalten.

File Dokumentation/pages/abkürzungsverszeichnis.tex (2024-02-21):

\newpage
\nonumsection{Abkürzungsverzeichnis}

\begin{acronym}[T3200]
	    \acro{ADC}{Analog Digital Converter}
        \acro{API}{Application Programming Interface}
        \acro{BLDC}{Brushless DC}
        \acro{CGI}{Common Gateway Interface}
        \acro{DAC}{Digital Analog Converter}
        \acro{DC}{Direct Current}
        \acro{DHCP}{Dynamic Host Configuration Protocol}
        \acro{FRAM}{Ferroelectric Random Access Memory}
        \acro{GPIO}{General-Purpose Input/Output}
        \acro{HTTP}{Hypertext Transfer Protocol}
        \acro{HTML}{Hypertext Markup Language}
        \acro{HTWG}{Hochschule für Technik, Wirtschaft und Gestaltung}
        \acro{IO}{Input Output}
        \acro{IP}{Internet Protocol}
        \acro{JSON}{Java Script Object Notation}
        \acro{LED}{Light Emitting Diode}
        \acro{LWIP}{Lightweight IP}
        \acro{MSB}{Most significant Bit}
        \acro{MISO}{Master In Slave Out}
        \acro{MOSI}{Master Out Slave In}
        \acro{NMEA}{National Marine Electronics Association}
        \acro{PCB}{Printed Circuit Board}
        \acro{REST}{Representational State Transfer}
        \acro{SMD}{Surface-Mount Device}
        \acro{SPI}{Serial Peripheral Interface}
        \acro{SSI}{Server Side Includes}
        \acro{TCP}{Transmission Control Protocol}
        \acro{UART}{Universal Asynchronous Receiver/Transmitter}
        \acro{URI}{Uniform Resource Identifier}
        \acro{URL}{Uniform Resource Locator}
        \acro{WP}{Write Protect}
        \acro{WREN}{Write Enable}
\end{acronym}

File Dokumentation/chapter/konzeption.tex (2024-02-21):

\newpage
\section{Hardware}
\begin{figure}[H]
	\centering
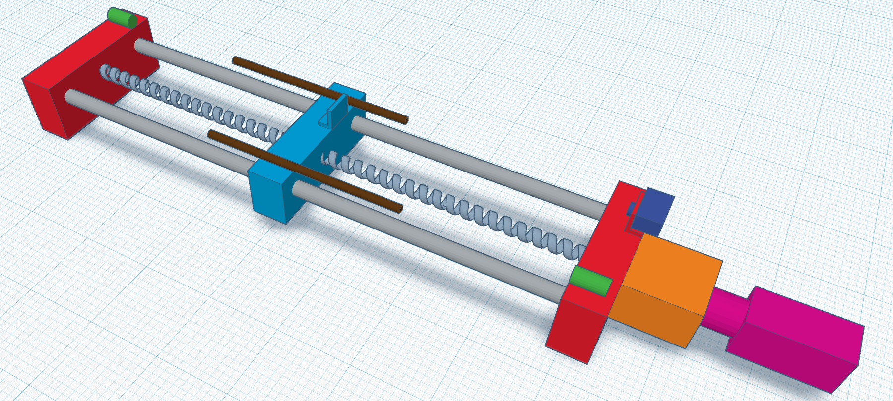
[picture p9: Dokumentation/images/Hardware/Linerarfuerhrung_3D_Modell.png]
	
	\caption{Simplifiziertes 3D Modell der Lineraführung}
	\label{fig:Systemaufbau}
\end{figure}
Da sich das Sailwind 4.0 Projekt noch in der Entwicklung befindet, existiert noch kein komplett zusammengebauter Prototyp in dem alle Teile des Projektes zusammenfinden. Die für diese Arbeit relevante Linearführung ist bereits als eigenständiges Objekt zusammengebaut und wie in \autoref{fig:Systemaufbau} zusehen, aufgebaut. Dabei wird die rotierende Bewegung eines BLDC Motors (Pink) mit der Hilfe eines Getriebes (Orange) und einer Gewindestange in eine translatorische Bewegung umgewandelt, mit welcher der Schlitten (Hellblau) zwischen den beiden stationären Punkten (Rot) hin und her bewegt werden kann. Die beiden Endschalter (Grün) dienen der Kollisionserkennung und können auch dazu genutzt werden, den Bewegungsraum einzuschränken. Dies gelingt durch das Verschieben der beiden Metallstangen (Braun), welche den Platz zwischen dem Schlitten und den stationären Elementen vorgeben. Zusätzlich kann über einen Abstandssensor (dunkel Blau) die Position des Schlittens in Relation zum Abstandssensor bestimmt werden.\\

\noindent Die Linearführung soll später dazu genutzt werden um die Segel des Windkraftwerkes zu trimmen und zu rollen (siehe Kapitel \ref{sec:principles}). Zusätzlich zu dem präsentierten Aufbau soll sich auf dem Schlitten zukünftig ein Druckkraftsensor befinden, der die Kraft auf die Rotorwelle messen soll. Dieser wurde allerdings zum Zeitpunkt der Arbeit noch nicht geliefert oder auf dem Prototypen angebracht. Getrennt vom Aufbau soll ebenfalls ein Anemometer an der Kuppel angebracht werden, das die Windrichtung und Geschwindigkeit misst.

%Hier erwähnen was Platine alles für Aufgaben hat
%Um die Segel des Windkraftwerkes jederzeit für maximale Effizienz eingestellt zu haben, müssen diese dynamisch Eingestellt werden können. Hierfür überwacht ein Controllino, die über Sensoren seine Umgebung und berechnet daraus die optimale Segel Einstellung. (KP sollte besser schon früher erwähnt werden/bzw wurde eventuell schon erwähnt)
\subsection{Ziele}
Die Hardware der Steuerung zu der eben vorgestellten Linearführung soll dabei folgende Aufgaben übernehemen:
\begin{itemize}
	\item Ansteuerung aller Sensoren und Aktoren
	\item Stromversorgung aller Komponenten
	\item Lokale Bedienung der Steuerung
	\item Ethernetkommunikation mit dem Controllino
\end{itemize}

\noindent Neben diesen Aufgaben soll die ganze Steuerung in einem zumindest Staub- und Spritzwassergeschützten Gehäuse untergebracht werden. Die Vorgängergruppe hatte sich dieser Aufgabe bereits gewidmet, allerdings wurde der resultierende Prototyp aufgrund der aufgetretenen Fehler und des zu großen Formfaktors nicht weiter verwendet. Diese Probleme sollen in dieser Iteration ebenfalls behoben werden.

%Bei dem Entwurf der Hardware sind mehrere Dinge zu beachten. Da das Sailwind 4.0 Projekt noch in den Startschuhen steht, sind einige dieser Faktoren auch noch nicht klar Bestimmbar zum Zeitpunkt dieser Arbeit. Aus diesem Grund wurden an manchen Stellen die Design Kriterien freier oder unnötig Komplex ausgelegt.\\
%
%Um die Steuerung der Segel zu ermöglichen wird ein System benötigt das alle nötigen Akteure und Sensoren, Ansteuret und Überwacht. Hierfür soll eine Steuerelektronik Hardware entworfen werden. Da sich diese im Außeneinsatz befindet sollte diese in einem Wasserdichten Gehäuse eingeschlossen sein. Eine vorrausgehende Gruppe hatte bereits die Steuerelektronik entworfen, diese war allerdings zu groß dimensioniert und hatte einige Fehler, weswegen ebenfalls ein kleinere Formfaktor und die Behebung der Probleme als Ziel gesetzt wurden. Die Steuerelektronik soll Manuell Bedienbar sein, wewegen am Gehäuse ebenfalls eine Bedienmöglichkeit existieren sollte.

\label{Analyze_der_Aktoren_und_Sensoren}
\subsection{Analyse der bestehenden Hardware Elemente}
Um eine geeignete Steuerplatine zu entwerfen, bedarf es einer Analyse der Steuerelemente, welche bereits von der vorhergegangenen Gruppe festgelegt wurden. Diese können in die Kategorien Sensoren und Aktoren gruppiert werden. Dabei wurden die benötigte Spannung und die Schnittstellen betrachtet. Die Schnittstellen geben an, wie mit dem jeweiligen Gerät kommuniziert werden kann und welche davon benötigt werden. Über die Spannung kann die Versorgungsspannung der Platine ausgewält werden und bereits ein Spannungspotenzial festgelegt werden.\\

\subsubsection{Sensoren}
Zu den Sensoren zählen die folgenden Komponenten:
\begin{itemize}
	\item Induktiver Endschalter: IFM IFS204
	\item Optischer Abstandssensor: IFM OGD580
	\item Anemometer: MESA WSWD
	\item Druckkraft-Sensor: Burster 8532
	\item Temperatursensor
\end{itemize}

\noindent\textbf{Induktiver Endschalter}\newline
Zwei der IFM IFS204 Endschalter sind im Design mit eingebaut. Sie funktionieren als PNP-Schließkontakt und geben an einem Ausgang ein digitales 24V Signal aus, sobald sie ausgelöst werden (vgl. \cite{IFS_204}, S.6). Dabei hat jeder Endschalter eine Betriebsspannung von 9-30V.\\

\noindent\textbf{Optischer Abstandssensor}\newline
Der Abstandssensor OGD580 funktioniert über einen Laser der vom Gerät ausgehend über eine Reflektive Fläche zu diesem zurückgeworfen wird. Der Abstandsensor verfügt über ein Display das den gemessenen Abstand anzeigt und über das Gerät konfigurierbar ist. Er hat ebenfalls eine Betriebspannung von 9-30V. Der Abstand wird über einen digitalen Ausgang, dem sog. IO-Link ausgegeben. Da mit diesem nur sehr umständlich Umgegange werden kann, wurde ein zusätzlicher IO-Link Konverter hinzugefügt. Der EIO104 konvertiert die digitale IO-Link Schnittstelle zu einer analogen 4-20mA Schnittstelle mit der einfacher Umgegangen werden kann.\\

\noindent\textbf{Anemometer}\\
Das WSWD Anemometer wird genutzt, um die Windrichtung und -geschwindigkeit zu messen. Dieses basiert auf einer 24V Versorgungsspannung. Es besitzt ebenfalls ein Heizelement, das die Verwendung bei sehr niedrigen Temperaturen ermöglicht. Dieses wird allerdings im Einsatzszenario und im Prototyp nicht benötigt. Die Schnittstellen des Anenometers sind abhängig von dessen Ausführung. In der verwendeten Ausführung, dem WSWD1, können die Daten neben einer analogen auch über eine Digitale RS485/RS422 Schnittstelle abgefragt werden. Die Werte können Analog entweder als 0/4-20/24mA Strom- oder als 0/2-8/10V Spannungssignal ausgegeben werden. Die Digitale Schnittstelle kann neben der Datenausgabe auch zur Konfiguration des Gerätes genutzt werden und bietet eine Vielzahl an Konfigurationsparametern und Übertragungsprotokollen an.\\

\noindent\textbf{Druckkraft-Sensor}\newline
Der Burster Druckkraft-Sensor war der einzige Sensor der zum Zeitpunkt der Arbeit noch nicht im Prototyp mit eingebaut wurde. Dieser wurde aber dennoch mit eingeplant. Der Druckkraft Sensor kann ebenfalls mit den typischen 24V betrieben werden. Die Messwerte werden hier über eine Analoges 0-10V Spannungssignal übertragen.\\

\noindent\textbf{Temperatursensor}\newline
Es gibt noch keine genaueren Informationen zu einem eventuell zum Einsatz kommenden Temperatursensor. Es wurde dennoch ein zusätzlicher analoger Eingang für eine entsprechende 4-20mA Schnittstelle eingeplant.\\
\subsubsection{Aktoren}
Zu den Aktoren zählen die folgenden Komponenten:
\begin{itemize}
	\item Gleichstrommotor: Dunkermotoren BG 45x30 SI
	\item Externe Relais
\end{itemize}

\noindent\textbf{Gleichstrommotor}\newline
Der Dunker BG 45x30 SI Gleichstrommotor ist die antreibende Kraft im Aufbau. Da der Motor eine interne Regelung besitzt, sind Leistungs- und Logikversorgung getrennt. Der Motor an sich wird dabei über den Leistungsteil bestromt, während der Logikteil für die Steuerung und die Bereitstellung von Feedback-Daten zuständig ist. Die Betriebsspannung der Leistungs- und Logikversorgung liegt bei 24V, wobei der Leistungsteil einem maximal zulässigen Dauerstrom von 3,8A ausgesetzt sein darf. Die Ansteuerung des Motors findet über vier digitale- und einen analogen Eingang statt. Der Motor stellt Feedback zum aktuellen Status über drei Ausgänge bereit. Diese geben die Drehrichtung, aktuelle Störungen und die Drehgeschwindigkeit des Motors in Impulsen an. Die Bezeichnung und Funktionen dieser Ein-/Ausgänge sind in \autoref{tab:digitale_Eingaenge}/\autoref{tab:andere_Ausgaenge} dargestellt.\\
% Please add the following required packages to your document preamble:
% \usepackage{graphicx}
\begin{table}[H]
	\centering
	\begin{tabular}{|c|c|c|}
		\hline
		\textbf{Eingang 1 (IN1)} & \textbf{Eingang 0 (IN0)} & \textbf{Funktion}      \\ \hline
		0                        & 0                        & Motor aus              \\ \hline
		0                        & 1                        & Linkslauf              \\ \hline
		1                        & 0                        & Rechtslauf             \\ \hline
		1                        & 1                        & Stopp mit Haltemoment  \\ \hline
		\textbf{Eingang 3 (IN3)} & \textbf{Eingang 2 (IN2)} &                        \\ \hline
		0                        & 0                        & Drehzahlvorgabe Analog \\ \hline
		0                        & 1                        & Stromvorgabe Analog    \\ \hline
		1                        & 0                        & Geschwindigkeit 1      \\ \hline
		1                        & 1                        & Geschwindigkeit 2      \\ \hline
	\end{tabular}%
	\caption{Eingänge und Funktionen des BG 45x30 SI (vgl. \cite{BG_45}, S.22)}
	\label{tab:digitale_Eingaenge}
\end{table}
\begin{table}[H]
	\centering
	\begin{tabular}{|c|c|c|}
		\hline
		\textbf{Name} & \textbf{Wertebereich} & \textbf{Funktion}      \\ \hline
		Analog In                & 0-4092$\frac{U}{min}$                        & Drehzahlvorgabe/            \\ & 0-10V & Analogwert \\ \hline		Out 1                & 12$\frac{Impulse}{U}$                        & Aktuelle Drehzahl             \\ \hline
		Out 2                & 1 = Störung; 0 = keine Störung                        &  Fehlerangabe            \\ \hline
		Out 3              & 1 = Linkslauf; 0 = Rechtslauf                       &  Drehrichtung           \\ \hline
	\end{tabular}%
	\caption{Analoger Eingang und Digitale Ausgänge des BG 45x30 SI (vgl. \cite{BG_45}, S.23)}
	\label{tab:andere_Ausgaenge}
\end{table}

\noindent\textbf{Externe Relais}\newline
Zum Zeitpunkt der Arbeit gab es noch keinen konkreten Verwendungszweck der zwei externen Relais, diese wurden für zusätzliche Funktionalitäten dennoch mit eingeplant und sollten über ein 24V Signal geschaltet werden. Sie könnten z.B zum Auslösen einer Motorbremse genutzt werden.\\

\noindent\textbf{Controllino}\newline
Der Controllino ist der zentrale Microcontroller und verwaltet alle Aktoren im fertigen Sailwind 4.0 Prototyp. Dieser kann nicht zu einen der beiden Kategorien gezählt werden, sollte hier aber dennoch kurz erwähnt werden. Von diesem soll das in der Arbeit zu entwerfende System seine Befehle zur Segelausrichtung empfangen. Der Datenaustausch soll dabei über Ethernet stattfinden, um die Distanz zwischen der Kuppel, in dem sich die Linearführung befindet und Basis in der sich der Controllino befindet, zu überbrücken. Zusätzlich dazu ist es geplant die Platine vom Controllino mit Strom zu versorgen.
\subsubsection{Zusammenfassung und Übersicht}
Damit sind nun alle externen Komponente im System abgedeckt. Die benötigte Spannungsversorgung sowie alle Schnittstellen sind in \autoref{tab:uebersicht-externe-elemente} dargestellt. Zusätzlich wurden die Verbindungen in einem Blockschaltbild in \autoref{fig:System_Aufbau} zusammengefasst, wobei alle blauen Pfeile die digitalen 24V Ein- und Ausgänge beschreiben.
\begin{figure}[H]
	\centering
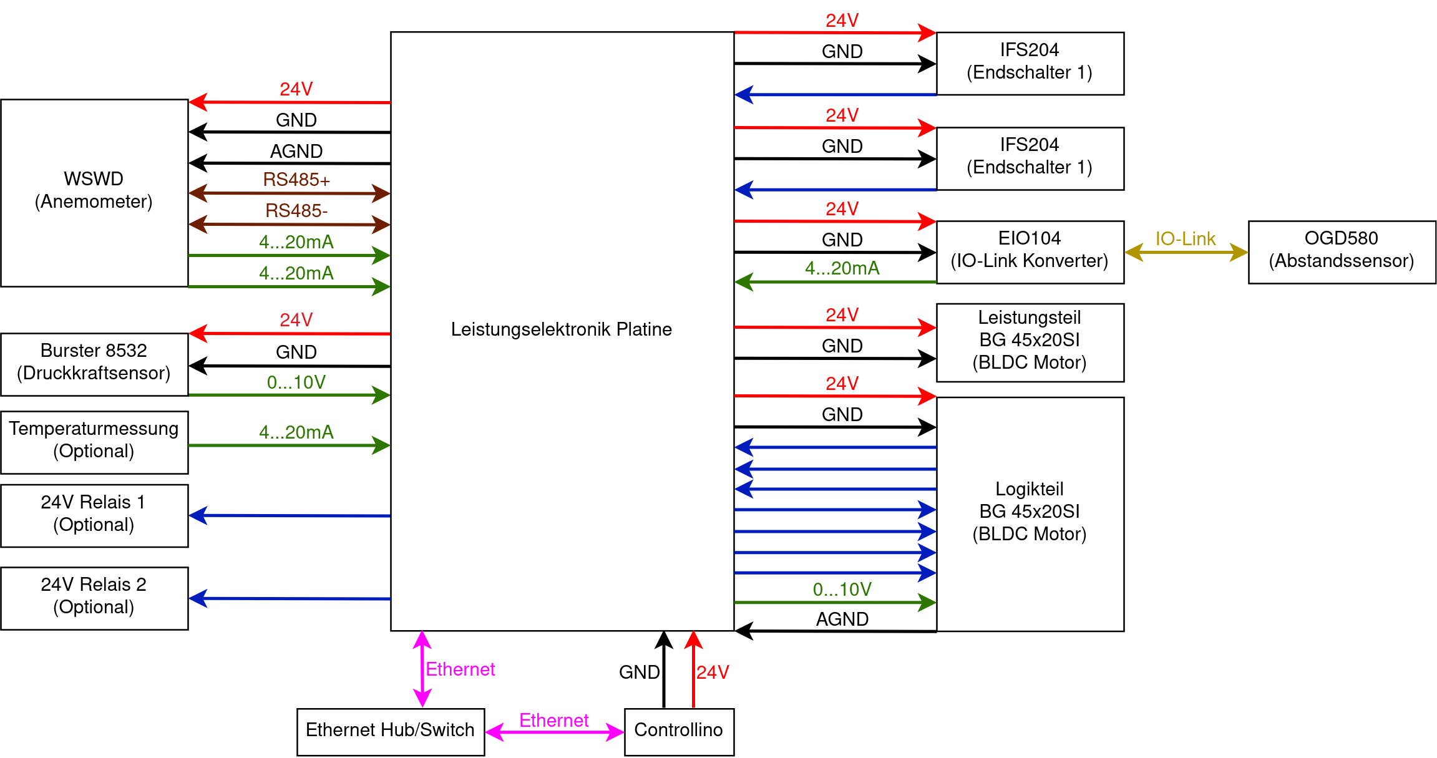
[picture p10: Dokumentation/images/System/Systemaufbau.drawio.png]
	
	\caption{Blockschaltbild der benötigten Ein- und Ausgänge der Platine}
	\label{fig:System_Aufbau}
\end{figure}
% Please add the following required packages to your document preamble:
% \usepackage{graphicx}
\begin{table}[H]
	\centering
	\resizebox{\textwidth}{!}{%
		\begin{tabular}{|l|lllllllllll|}
			\hline
			\textbf{Element} & \multicolumn{11}{l|}{\textbf{Pinout}} \\ \hline
			\textbf{Endschalter 1} & \multicolumn{1}{l|}{24V} & \multicolumn{1}{l|}{GND} & \multicolumn{1}{l|}{OUT} & \multicolumn{8}{l|}{} \\ \hline
			\textbf{Endschalter 2} & \multicolumn{1}{l|}{24V} & \multicolumn{1}{l|}{GND} & \multicolumn{1}{l|}{OUT} & \multicolumn{8}{l|}{} \\ \hline
			\textbf{Abstandssensor} & \multicolumn{1}{l|}{24V} & \multicolumn{1}{l|}{GND} & \multicolumn{1}{l|}{IO-Link} & \multicolumn{8}{l|}{} \\ \hline
			\textbf{IO-Link Konveter} & \multicolumn{1}{l|}{24V} & \multicolumn{1}{l|}{GND} & \multicolumn{1}{l|}{AOUT} & \multicolumn{8}{l|}{} \\ \hline
			\textbf{Anemometer} & \multicolumn{1}{l|}{24V} & \multicolumn{1}{l|}{GND} & \multicolumn{1}{l|}{AOUT} & \multicolumn{1}{l|}{AOUT} & \multicolumn{1}{l|}{AGND} & \multicolumn{1}{l|}{RS485+} & \multicolumn{1}{l|}{RS485-} & \multicolumn{4}{l|}{} \\ \hline
			\textbf{Druckkraftsensor} & \multicolumn{1}{l|}{24V} & \multicolumn{1}{l|}{GND} & \multicolumn{1}{l|}{AOUT} & \multicolumn{1}{l|}{AGND} & \multicolumn{7}{l|}{} \\ \hline
			\textbf{Motor Leistung} & \multicolumn{1}{l|}{24V} & \multicolumn{1}{l|}{GND} & \multicolumn{9}{l|}{} \\ \hline
			\textbf{Motor Logik} & \multicolumn{1}{l|}{24V} & \multicolumn{1}{l|}{GND} & \multicolumn{1}{l|}{IN0} & \multicolumn{1}{l|}{IN1} & \multicolumn{1}{l|}{IN2} & \multicolumn{1}{l|}{IN3} & \multicolumn{1}{l|}{AIN} & \multicolumn{1}{l|}{AGND} & \multicolumn{1}{l|}{OUT1} & \multicolumn{1}{l|}{OUT2} & OUT3 \\ \hline
			\textbf{Externes Relais 1} & \multicolumn{1}{l|}{OUT} & \multicolumn{1}{l|}{GND} & \multicolumn{9}{l|}{} \\ \hline
			\textbf{Externes Relais 2} & \multicolumn{1}{l|}{OUT} & \multicolumn{1}{l|}{GND} & \multicolumn{9}{l|}{} \\
			\hline
			\textbf{Temperatur Sensor} & \multicolumn{1}{l|}{AOUT} & \multicolumn{10}{l|}{} \\ \hline
			\textbf{Controllino} & \multicolumn{1}{l|}{Ethernet} & \multicolumn{10}{l|}{} \\ \hline
		\end{tabular}%
	}
	\caption{Übersicht Stromversorgung und Schnittstellen der externen Elemente}
	\label{tab:uebersicht-externe-elemente}
\end{table}
\subsection{Auswahl der Platinen Bauteile}
Da nun klar ist, welche Anforderungen durch die anzuschließenden Geräte bestehen, kann auf Basis dieser weiter verfahren werden. Dabei soll im folgenden ein geeigneter Mikrocontroller, sowie die nötigen Platinenkomponenten ausgewählt werden, um mit den Sensoren und Aktoren zu kommunizieren und diese mit Strom zu versorgen.
\subsubsection{Mikrocontroller}
Die Auswahl des Mikrocontrollers wurde auf der Basis folgender Kriterien beschlossen:
\begin{itemize}
	\item Benötigte Inputs und Outputs
	\item Softwaresupport 
	\item Entwicklung
	\item Verfügbarkeit
\end{itemize}
Dabei gab es die Option, den Chip als einzelnes Element direkt in der selbst erstellten Platine einzubetten oder ein Entwicklungsboard zusammen mit einer Erweiterungsplatine zu nutzen. Schließlich fiel die Entscheidung auf die Verwendung eines Entwicklungsboards, um bereits parallel zum Hardwaredesign eine geeignete Software entwickeln und mit prototypischen Aufbauten testen zu können. Dies bot ebenfalls den Vorteil, dass ein kaputter Chip schnell ersetzt werden kann und mit der Platine ein möglicher Formfaktor für die Erweiterung vorgegeben ist. Außerdem kann durch den integrierten Debugger schneller neue Software getestet und aufgespielt werden. Zuletzt besitzen viele Entwicklungsboards bereits einen Ethernet-Port, der somit nicht mehr extra bestellt werden müsste.\\

\noindent Aufgrund der oben genannten Kriterien und der Entscheidung, ein Entwicklungsboard zu benutzen viel die Wahl auf das STM32 NUCLEO F439zi Board. Dieses war bereits an der HTWG Konstanz verfügbar und ist mit dem Softwaresupport der Firma ST, welche insbesondere eine eigene Entwicklungsumgebung anbietet, einfach zu programmieren und aufzusetzen. Außerdem enthalten Entwicklungsboards von ST einen abbrechbaren Debugger, womit das Board auch außerhalb der Entwicklungsphase eingesetzt werden kann.
\subsubsection{Relais}
Um das Auslösen eines Endschalters an den Mikrocontroller weiterzugeben, werden zwei 24V Relais benötigt, die bei Aktivierung der Spule ein 3,3V Signal an den Eingang des Mikrocontrollers weitergeben. Gleichzeitig soll durch die Relais der Eingang 1 oder 2 des Motors auf Null gesetzt werden. Diese geben die Drehrichtung vor und stoppen den Motor, sobald beide auf null gesetzt sind. Da dieses System unabhängig von der Software des Mikrocontrollers agiert, bietet es eine zusätzliche Sicherheit gegenüber Beschädigungen an der Linearführung aufgrund von Programm-Fehlfunktionen. Hierfür wurden die Omron G6S-2F 24DC Relais ausgewählt. Diese besitzen zwei schaltbare Ausgänge und weisen einen kompakten Formfaktor auf.
\subsubsection{Optokoppler}
Um die restlichen 24V Ein- und Ausgänge zu steuern oder auszulesen, kommen Optokoppler zum Einsatz. Diese isolieren ähnlich zu Relais den 24V und 3,3V Schaltkreis. Davon werden insgesamt neun benötigt, um die digitalen Ein- und Ausgänge des Motors und die beiden externen Relais zu schalten. Zusätzlich sollte wie bei den Relais wieder ein kleiner Formfaktor vorliegen. Hierfür wurden die LTV-817S ausgesucht. Deren typische Schaltzeit von 3-18$\mu$s ist für die Anwendung ausreichend und durch den Formfaktor lassen sich die Optokoppler gut auf der Platine unterbringen.
\subsubsection{RS485 zu UART Konverter}
Um das Anemometer über die RS485 Schnittstelle zu konfigurieren und Daten abzufragen wird ein zusätzlicher Baustein benötigt. Dieser konvertiert das differenzielle RS485-Signal zu einem nicht differenziellen \ac{UART}-Signal, welches der Mikrocontroller verarbeiten kann. Hierfür wurde der MAX3485CSA+CT-ND ausgesucht, da dieser mit einer 3,3V Versorgungsspannung betrieben werden kann und eine Datenübertragungsrate von bis zu 10$\frac{MB}{s}$ unterstützt.
\subsubsection{FRAM}
Da die neutrale Position des Segels dauerhaft gespeichert werden soll, wird ein nicht flüchtiger Speicherstein benötigt. Dabei ist \ac{FRAM} eine der billigsten Speichermöglichkeiten für diesen Zweck. Es wurde die geringste Speichergröße gewählt, da die gespeicherten Daten jederzeit, wie bei einem EEPROM Speicher, überschrieben werden können. Hier wurde der FM25L16B-GTR gewählt, welcher mit einer Speicherkapazität von 16Kbit ausgestattet ist und damit für das Speichern der Positionsdaten geeignet ist. Da er über eine \ac{SPI} Schnittstelle angesteuert wird, sind schnelle Schreib- und Lesegeschwindigkeiten möglich, was für das regelmäßige Aktualisieren der Positionsdaten erforderlich ist. Ebenfalls ist die Lebenserwartung des Speichers von 85 Jahren unter Betrieb mit einer Taktfrequenz von 20Mhz mehr als ausreichend.
\subsubsection{Operations Verstärker}
Um die Drehzahl des Motors vorgeben zu können, wird ein analoges Signal im Bereich von 0-10V benötigt. Da der \ac{DAC} des Mikrocontrollers bei einer Versorgungsspannung von 5V maximal ein analoges Signal von 3,3V ausgeben kann \cite{STM32}, wird ein Operationsverstärker benötigt. Dieser soll mit einer 24V Offsetspannung das Ausgangssignal auf 10V skalieren. Hier gab es bis auf die Maximalspannung keine besonderen Anforderungen an den Operationsverstärker und somit wurde der weitverbreitete LM2904QS ausgewählt.
\subsubsection{DC/DC-Wandler}
Um alle Komponenten zu versorgen, bedarf es insgesamt drei verschiedenen Spannungspotenzialen: 24V, 5V und 3,3V. Dabei werden alle externen Steuerelemente direkt mit 24V versorgt. Der Mikrocontroller benötigt eine 5V Spannung, damit dieser auch ohne Stromversorgung des Debuggers betrieben werden kann. Hierfür wird ein Step-Down Konverter genutzt, der die 24V Versorgungsspannung auf 5V herunterbricht. Die 5V müssen zusätzlich mit einem Festspannungsregler auf 3,3V-Level konvertiert werden, um die übrigen Bauteile zu versorgen. Bei der Auswahl wurde darauf geachtet, dass der Konverter einen ausreichenden Strom zu Verfügung stellt, ohne dabei dauerhaft unter Vollast zu laufen. Insbesondere muss hier der Verbrauch des Mikrocontrollers von bis zu 120mA (vgl. \cite{STM32_Electrical} S.103) eingerechnet werden. Unter der Annahme, dass die restlichen Bauteile nicht mehr als zusätzliche 380mA verbrauchen, wurde der R-78E5.0-0.5 ausgewählt. Dieser stellt bis zu 0,5A zur Verfügung und kann bei Bedarf durch eine 1A Version ausgetauscht werden. Als Festspannungsregler wurde der LM3940IMP-3.3 gewählt. Dieser kann Eingangsspannung von bis zu 7.5V in eine Ausgangsspannung von 3,3V umwandeln und hat dabei einen Durchsatz Strom von bis zu 1A. Damit genügt er den Anforderungen.
\subsubsection{Stromsensor}
Zur Überwachung des Motor Stroms kommt ein Hall-Stromsensor zum Einsatz. Dieser ist im Gegensatz zu einem resistiven Sensor genauer und isoliert den 24V und 3,3V Schaltkreis wie z.B im Schaltplan in \autoref{fig:Stromsensor} zusehen ist. 
\begin{figure}[H]
	\centering
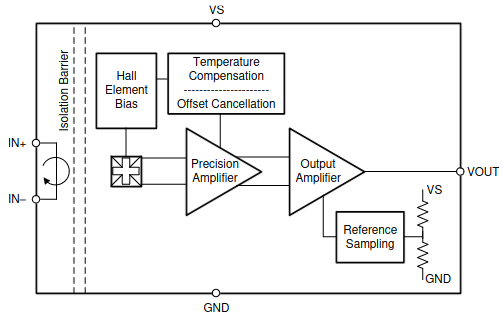
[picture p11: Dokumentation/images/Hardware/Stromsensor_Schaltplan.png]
	
	\caption{Schaltplan des Texas Instruments TMCS1101 Hall Stromsensor (vgl. \cite{Stromsensor_texas}, S.24)}
	\label{fig:Stromsensor}
\end{figure}
Er sollte in der Lage sein, den maximal zulässigen Motorstrom messen zu können. Da die meisten Hall Sensoren einen deutlich größeren Messbereich unterstützen, wurde der TMCS1101A3BQDRQ1 gewählt. Dieser kann einen maximalen Strom von $\pm$11,25A messen. Der gemessene Strom wird dabei als analoges 0-3,3V Signal ausgegeben und ist damit für diese Anwendung geeignet.
\subsubsection{Konnektoren}
Die externen Komponenten sollen über Schraubklemmen direkt an die Platine angeschlossen werden. Je nach Querschnitt der Kabel wurde ein größeres oder kleineres Rastermaß gewählt, um Platz auf der Platine einzusparen. Dabei wurde ein Standard Rastermaß von 2,54mm festgelegt und für die Kabel mit größerem Durchschnitt ein Rastermaß von 3,5mm.

\subsection{Gehäusebauteile}
Um die Platine, welche sich später in der Kuppel befinden soll, vor z.B Staub und Wasser zu schützen, soll diese in einem Gehäuse untergebracht werden. Das Gehäuse sollte eine Möglichkeit bieten, die Platine so zu platzieren und zu befestigen, dass im Innenraum noch genügend Platz für Kabelanschlüsse ist. Außerdem muss die Oberfläche des Gehäuses groß genug sein, um Bedienelemente und Status LEDs darauf komfortabel verteilen zu können. Den Anforderungen zufolge wurde das Modell Hammond Manufacturing RP1465 gewählt.
\begin{figure}[H]
	\centering
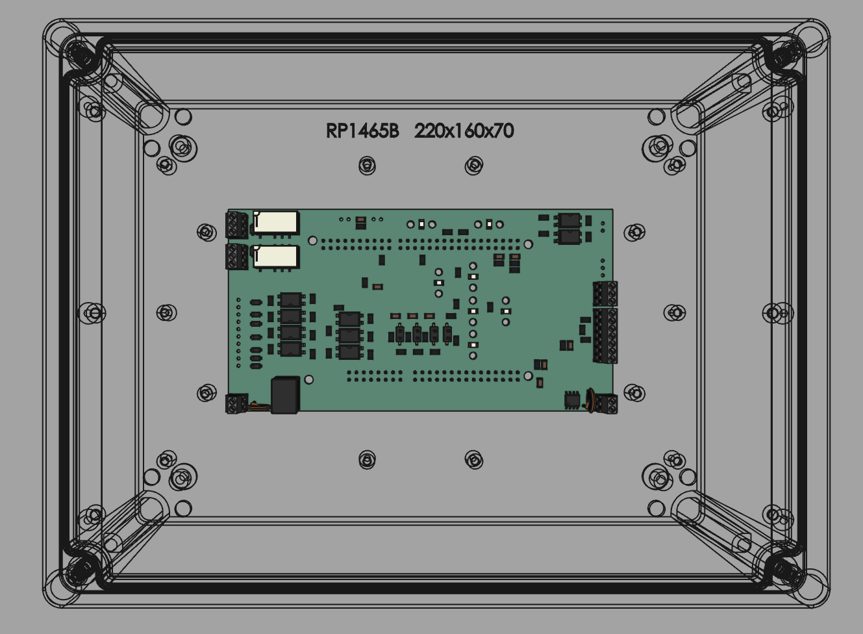
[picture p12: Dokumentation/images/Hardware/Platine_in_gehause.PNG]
	
	\caption{3D Modell der Platine innerhalb des Gehäuses}
	\label{fig:Gehaues_und_Platine}
\end{figure}
\noindent Wie in \autoref{fig:Gehaues_und_Platine} zusehen ist, bietet dieses genügend Platz für die Platine und alle Kabeldurchführungen. Es ermöglicht ebenfalls den Einsatz eines zweiten Bodens auf dem die Platine mit einer 3D gedruckten Befestigung angeschraubt werden können.\\

\subsubsection{Bedienoberfläche}
\noindent Die Bedienoberfläche besteht aus einer Reihe von Kippschaltern, Knöpfen und \ac{LED}s. Diese sind in \autoref{fig:Bedienung} dargestellt. Mit dem rechten Knopf soll zur Initialisierung des Systems eine automatische Kalibrierungsfahrt eingeleitet werden. Zusätzlich kann der Benutzer anschließend über die Trimm- und Rollknöpfe die Grenze zwischen diesen Bereichen (siehe \autoref{fig:powerCurve}) selbst anfahren und mit erneuter Betätigung des rechten Knopfes festlegen bzw. speichern. Danach kann mittels des Kippschalters in den Automatikbetrieb gewechselt werden, in dem die Steuerung vom Controllino übernommen und das Betätigen der Knöpfe folglich ignoriert wird.
Eine Reihe von LEDs gibt Feedback über den aktuellen Zustand der Linearführung. Dabei wird konstant der aktuelle Betriebsmodus durch zwei LEDs angegeben. Ebenfalls wird die Position relativ zur festgelegten neutralen Position durch zwei gelbe LEDs angegeben. Vom System selbst identifizierte Störungen werden durch eine rote LED signalisiert.\\
Die Knöpfe und Kippschalter sind jeweils mit Dichtungsringen spritzwassergeschützt am Gehäuse montiert. Die Kabel werden über Dupont-Stecker an der Platine angeschlossen. Im Gegensatz dazu sind die LEDs direkt auf der Platine platziert, wobei deren Strahlung durch flexible Lichtleiter zur Außenseite des Gehäuses geführt werden.
\begin{figure}[H]
	\centering
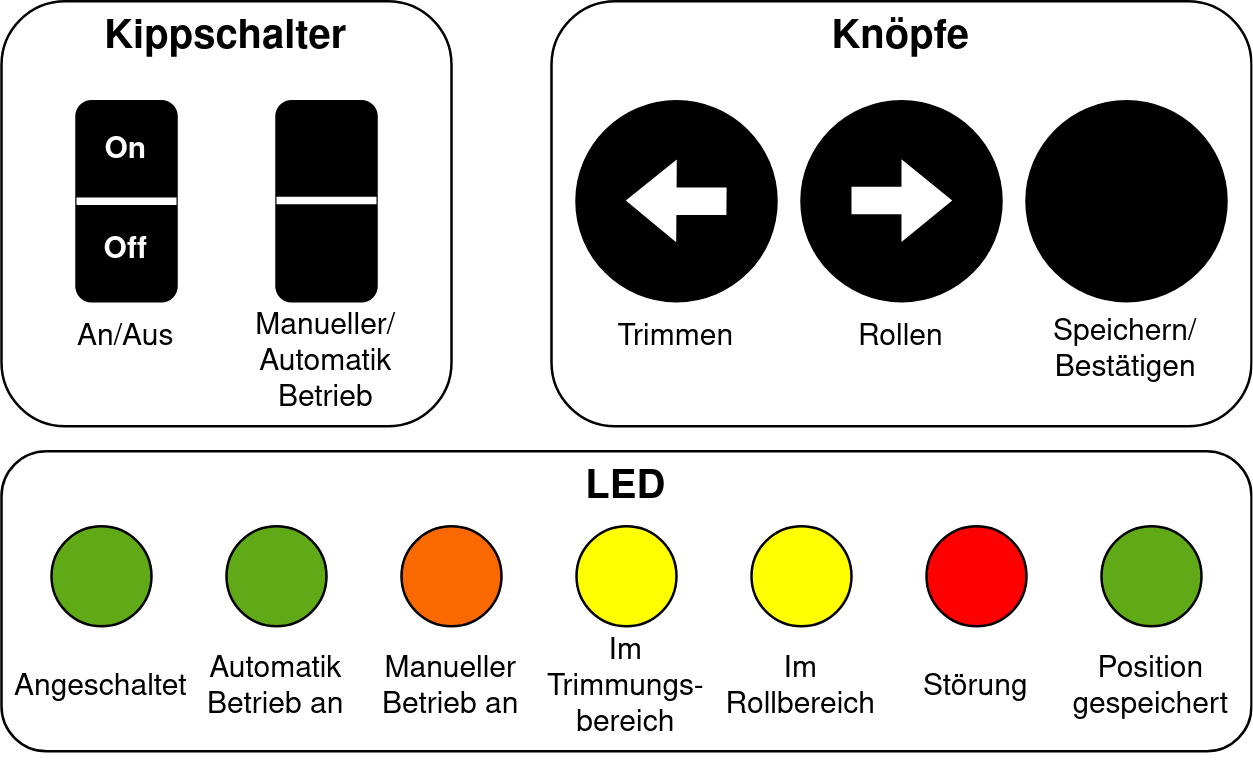
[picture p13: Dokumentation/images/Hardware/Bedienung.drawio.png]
	
	\caption{Bedienoberfläche der Segel Steuerung}
	\label{fig:Bedienung}
\end{figure}
\subsubsection{Kabelverschaubungen}
Um die benötigten Kabel zur Platine zuführen, wurden Kabelverschraubungen in die Seiten des Gehäuses eingelassen. In diese können die isolierten Kabel eingeführt und die Adernkabel an die richtige Position innerhalb des Gehäuses verlegt werden. Die Kabelverschraubungen sorgen nebenbei für eine Zugentlastung der Kabel.
\subsection{Platinen Schaltplan}
\begin{figure}[H]
	\centering
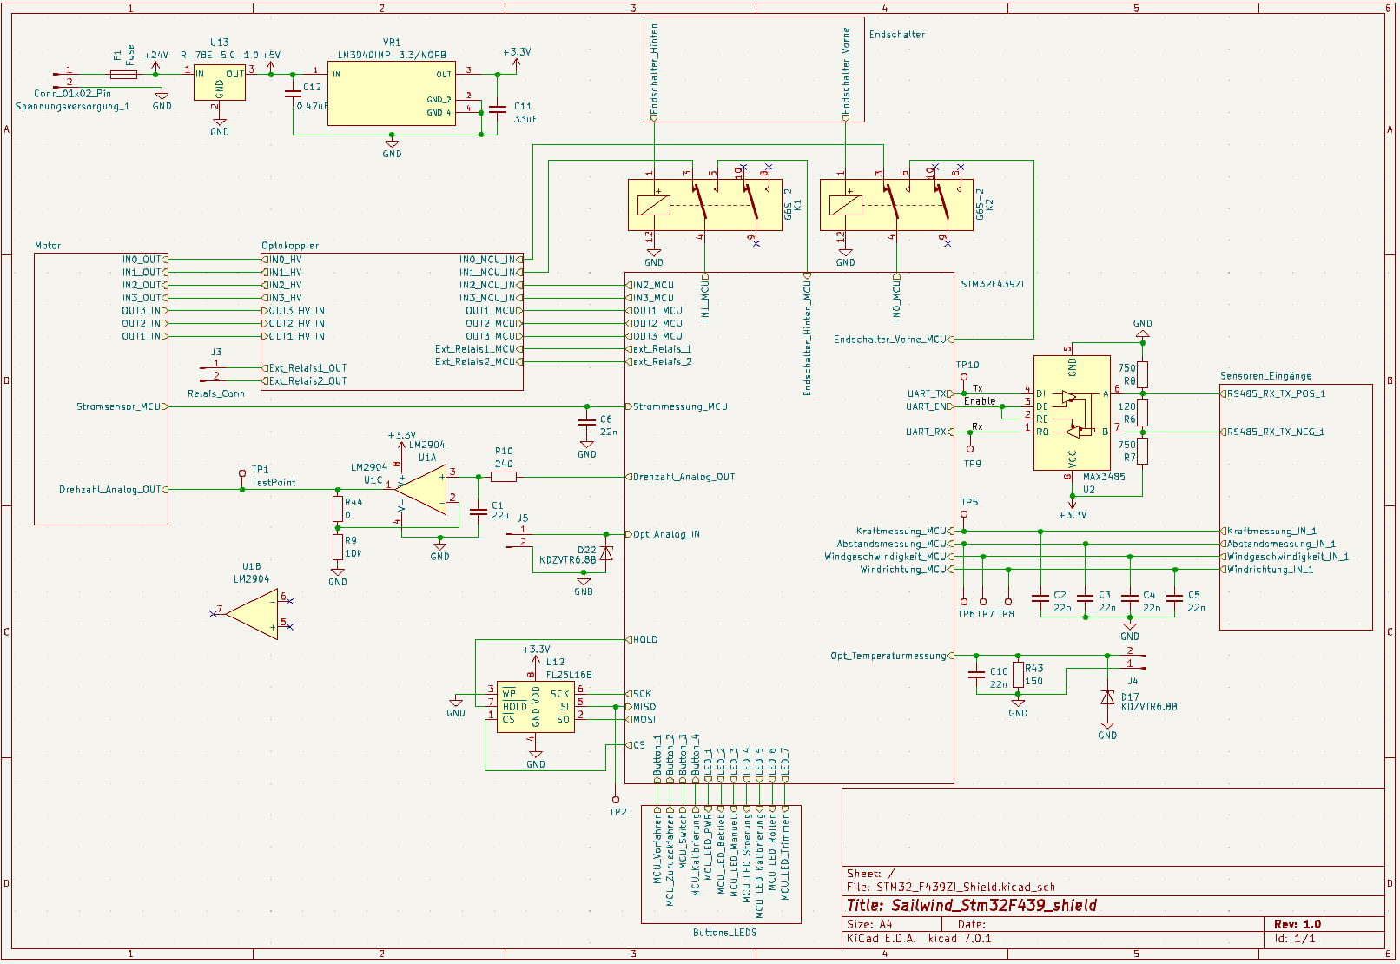
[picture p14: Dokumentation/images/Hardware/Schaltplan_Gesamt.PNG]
	
	\caption{Gesamtschaltplan der Platine}
	\label{fig:Schaltplan_gesamt}
\end{figure}
Eine Übersicht des Schaltplans ist in \autoref{fig:Schaltplan_gesamt} zusehen. Der komplette Schaltplan ist als KiCad Datei in der ZIP-Datei enthalten und ebenfalls in \autoref{sec:Schaltplan} hinterlegt. Der Schaltplan ist in unterschiedliche Bereiche eingeteilt, welche die Gruppierung der Komponenten wiedergeben. Dabei ist die STM32-Gruppe zentral positioniert und alle Bauteile und Komponenten um diese herum verteilt. Bauteile, die nur einfach verbaut sind wie z.B der FL25L16B \ac{FRAM} (Unten Links) wurden nicht in Gruppen eingeteilt, sondern direkt in der Gesamtansicht positioniert. Oben links befindet sich die Spannungsversorgung der Platine und die \ac{DC}/DC Wandler. Oberhalb des STM32 befinden sich die beiden Relais, welche mit den Endschaltern verbunden sind. Links außen befindet sich der \ac{BLDC} Motor, welcher mit dem Operationsverstärker und den Optokopplern verbunden ist. Rechts befinden sich mit Ausnahme des Stromsensors alle analogen Sensoren. Dort ist ebenfalls der MAX3485 \ac{UART} Konvertierer abgebildet. Unterhalb des Mikrocontrollers befinden sich die Knöpfe und LEDS, die das \ac{HMI} bilden. Im folgenden werden exemplarisch die Schaltungen für diese Gruppen genauer betrachtet.
\subsubsection{STM32F439zi Gruppe}
Der STM32F439zi enthält alle Pins, auf denen später die Erweiterungsplatine aufsitzt. Hier wurden alle benötigten Pins nach außen zur Schaltplanübersicht geführt.
\subsubsection{Motor Gruppe}
\begin{figure}[H]
	\centering
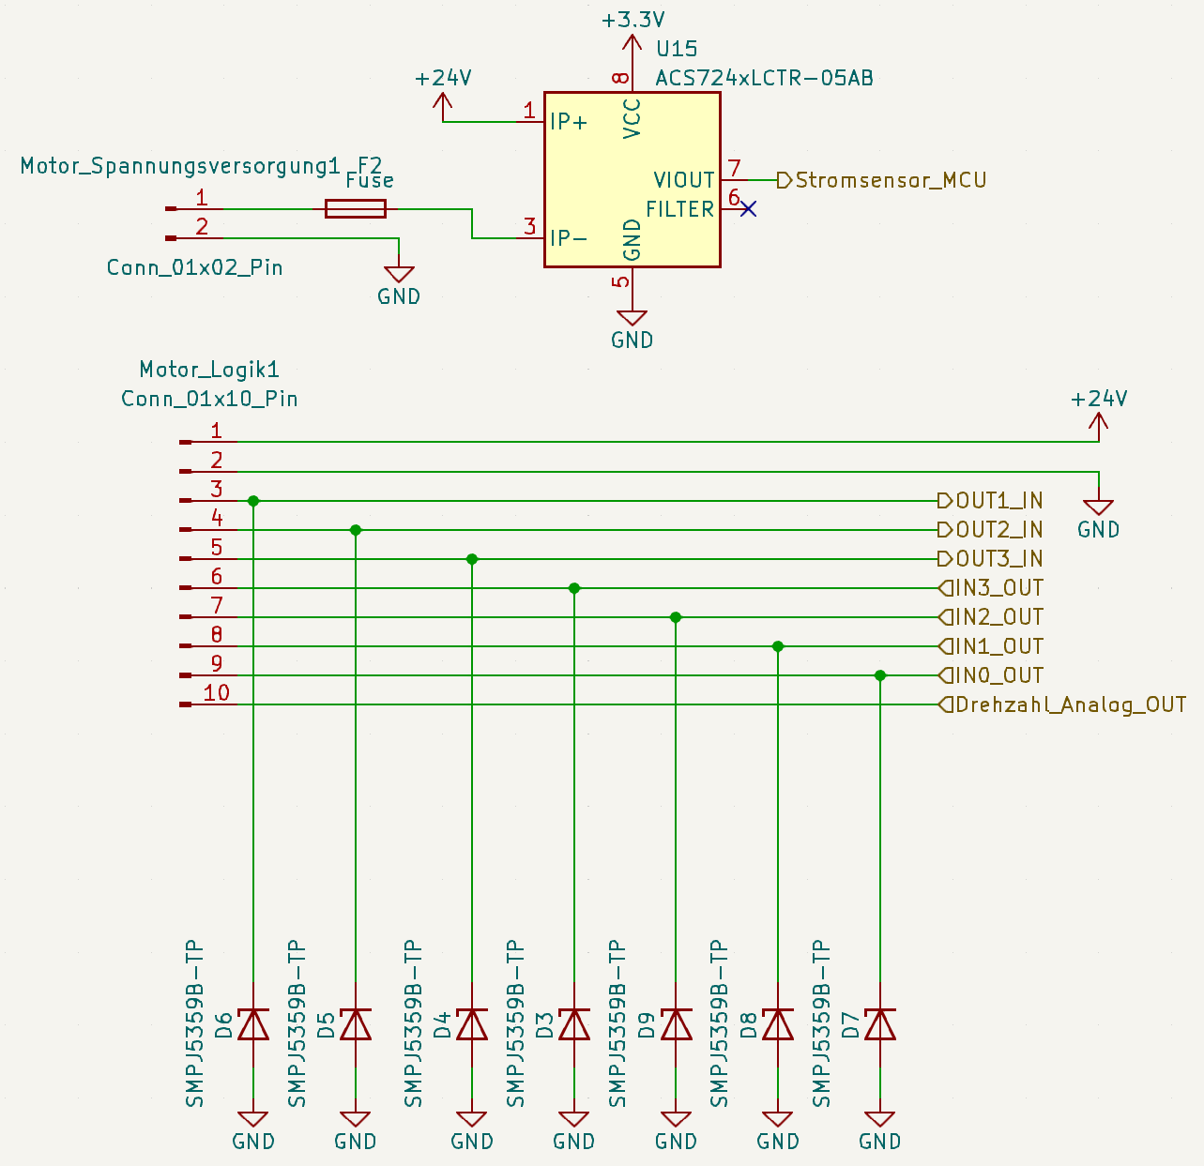
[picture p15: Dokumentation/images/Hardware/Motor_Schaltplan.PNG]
	
	\caption{Schaltplan der Motorgruppe}
	\label{fig:Motor_gruppe}
\end{figure}
In der Motorgruppe ist neben den Ein- und Ausgängen des BG 45x30 SI auch der Hall-Stromsensor abgebildet. Alle digitalen Ein- und Ausgänge auch außerhalb der Motorgruppe sind durch 24V Zener Dioden verschaltet, die als Überspannungsschutz agieren. Die Spannungsversorgungen der Platine und des Motors sind zusätzlich durch Überstromsicherungen geschützt, wie anhand des Stromsensors in \autoref{fig:Motor_gruppe} zu sehen ist.
\subsubsection{Optokoppler Gruppe}
\begin{figure}[H]
	\centering
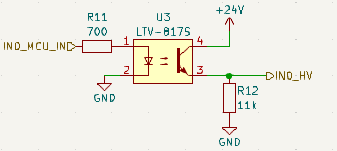
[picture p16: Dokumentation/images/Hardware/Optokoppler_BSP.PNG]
	
	\caption{Beispielhafte Schaltung eines Optokopplers}
	\label{fig:Optokoppler_gruppe}
\end{figure}
Alle Optokopplerschaltungen der Gruppe sind gleich aufgebaut. Eine beispielhafte Schaltung ist deswegen in \autoref{fig:Optokoppler_gruppe} dargestellt. Der Eingangswiderstand (links) begrenzt den Strom, welcher in der verbauten Infrarot-LED des Optokopplers den Stromfluss auf der Ausgangsseite bestimmt. Ein Pulldown-Widerstand auf der Ausgangsseite begrenzt den maximal erlaubten Strom zum Mikrocontroller und setzt den Eingang auf ein festgelegtes Potenzial.
\subsubsection{Sensoren Gruppe}
In der Sensoren Gruppe sind die analogen Sensoren abgebildet. Hier ist wie beispielhaft für den Abstandssensor in \autoref{fig:Eingang_bsp} gut zu erkennen, wie die Stromsignale in Spannungssignale von einem Widerstand umgewandelt werden. Für die 4-20mA Signale wurde dabei ein 150$\Omega$ Widerstand gewählt, da damit bei einem maximalen Strom von 20mA annähernd 3,3V erreicht werden:
\begin{equation}
	U = 20mA\times150\Omega = 3V
\end{equation}
Zum Überspannungsschutz ist hier ebenfalls eine Zener Diode mit einer Durchbruchspannung von 6,8V angebracht.
Das Spannungssignal von dem Druckkraftsensor wird durch einen Spannungsteiler ebenfalls auf 0-3V skaliert:
\begin{equation}
	U_{Ausgang} = \frac{10V}{2300\Omega + 1000\Omega}\times1000\Omega = 3,03V
\end{equation}
Um die analogen Signale stabiler zu halten und niedrige Frequenzen zu entfernen, wurden für jedes analoge Signal zusätzlich Keramikpufferkondensatoren mit einer Kapazität von 22nF hinzugefügt.
\begin{figure}[H]
	\centering
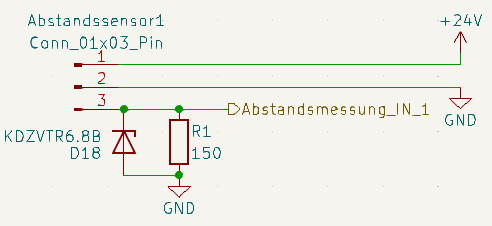
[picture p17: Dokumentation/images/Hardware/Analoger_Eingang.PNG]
	
		\caption{Schaltplan des analogen Eingangs des Abstandsensors}
	\label{fig:Eingang_bsp}
\end{figure}
\subsubsection{Buttons und LEDs Gruppe}
Damit der Effekt des Debouncing nicht über die Software ausgeregelt werden muss, wurde für die Buttons eine entsprechende Schaltung integriert. Hierbei wurde ein RC-Filter, wie in \autoref{fig:RC_Filter_Knopf} zusehen, genutzt. Beim Drücken des Knopfes wird der Kondensator zuerst entladen, was zu einer langsam abfallend Spannung führt. Wird der Knopf losgelassen, lädt sich dieser wieder auf. Somit werden jegliche unerwünschte Spannungssprünge vollständig unterdrückt. Da die Debounce-Zeit der Knöpfe typischerweise bei 0,1ms liegt (vgl. \cite{Schurter_Knopf}, S.2), wurde eine Zeitkonstante $\tau$ = 10ms für den RC Filter angenommen. Die \ac{LED}s wurden je nach zulässigem Strom mit einem entsprechenden Widerstand versehen.
\begin{figure}[H]
	\centering
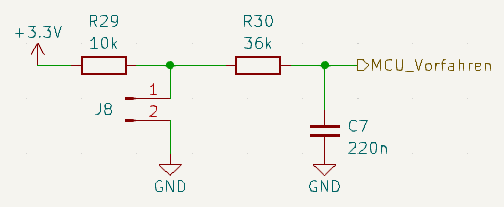
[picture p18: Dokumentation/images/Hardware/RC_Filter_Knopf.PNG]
	
	\caption{RC-Filter für einen am Gehäuse angebrachten Knopf}
	\label{fig:RC_Filter_Knopf}
\end{figure}
\subsection{\ac{PCB}}
Das fertige PCB ist als 3D Modell in \autoref{fig:PCB_3D} dargestellt. Beim Entwurf wurde darauf geachtet, die 24V- von den 3,3V-Komponenten zu trennen, um die Beeinflussung analoger Signale durch große Ströme oder höhere Frequenzen so weit wie möglich zu reduzieren. Aus diesem Grund befinden sich die 24V-Komponenten am Rand der Platine, während die 3,3V-Bauteile weitestgehend im Inneren der Platine positioniert sind. Die Platine sitzt mit vier unterschiedlichen Pin-Reihen am Entwicklungsboard auf und führt diese auf die Oberseite. Die Spurbreiten auf der Platine wurden aufgrund von Stromflüssen, Spannungen und Längen bestimmt. Da der Platinenhersteller eine minimale Spurbreite von 0,2mm vorgibt, reichte diese für fast alle Spuren aus. Eine Ausnahme bildet jene, welche dem Motorstrom von bis zu 4A ausgesetzt ist und dementsprechend breiter ausgelegt werden musste. 
\begin{figure}[H]
	\centering
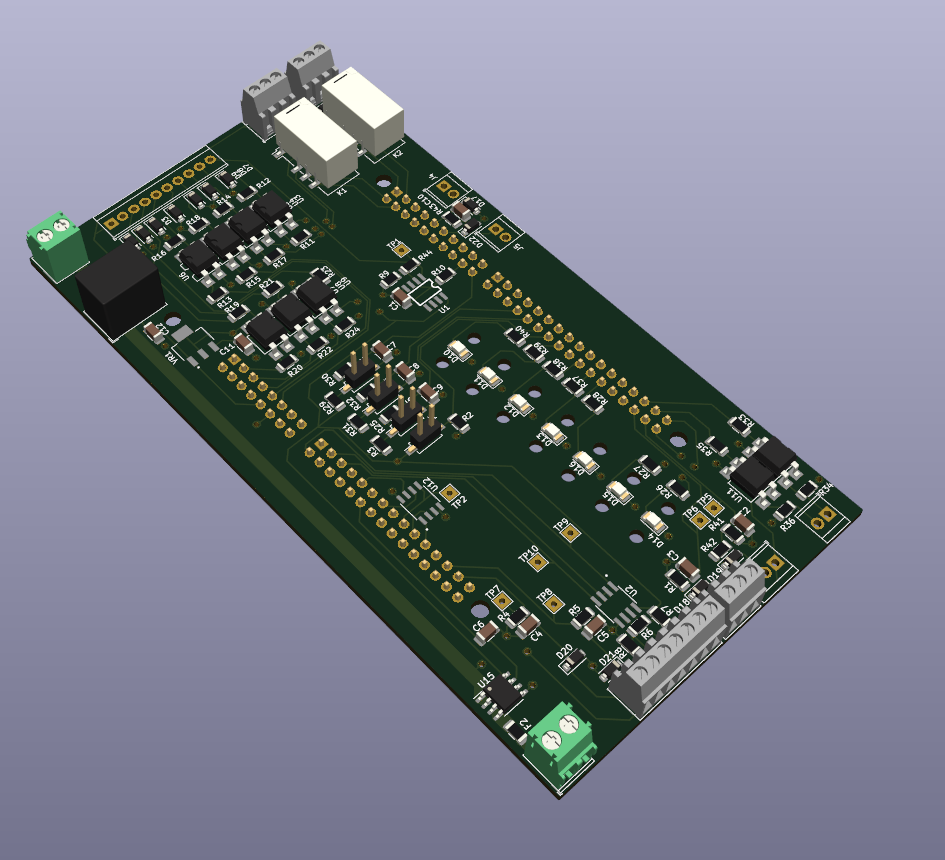
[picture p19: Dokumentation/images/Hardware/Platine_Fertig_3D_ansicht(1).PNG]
	
	\caption{3D Ansicht des fertigen PCBs}
	\label{fig:PCB_3D}
\end{figure}
Der Formfaktor der Platine wurde an dem Standard Layout eines ST Nucleo 144 Boards orientiert. Aufgrund des damit verfügbaren Platzes wurden ausschließlich \ac{SMD} Bauteile der Größe 1206 verwendet. Diese sind groß genug, um sie unter angemessenem Aufwand von Hand zu löten und andererseits klein genug, um geeignete Abstände bei der Positionierung einhalten zu können. Eine Liste aller verwendeter Platinen- und Gehäusebauteile ist in \autoref{sec:Bauteilliste} zu finden.

\subsection{Probleme}
Während der Nutzung und Bestückung des \ac{PCB}s sind einige Probleme aufgetreten, die auf das Design oder falsche Berechnungen zurückzuführen sind. Diese sollen im folgenden erklärt und korrigiert werden.
\subsubsection{Schraubklemmen Löcher}
Der erste Fehler, welcher zu Beginn auffiel, waren die Lochdurchmesser für die Schraubklemmen. Diese waren zwar groß genug dimensioniert, um die Pins der Schraubklemmen durchzuführen, jedoch fehlte damit der Platz, um Nieten zur elektrischen Verbindung zwischen den Pins und der Platine einzufügen. Die Löcher waren ebenfalls zu klein, um mit Drähten eine Verbindung zwischen dem Pin und den Spuren herzustellen. Dies führte zu vielen elektrischen Kontaktverlusten und minderte die horizontale Stabilität der Schraubklemmen. Die Kontaktverluste führten wiederum zur mangelnden Präzision der analogen Eingänge (siehe \autoref{Mangelnde_Präzision}). Da die Löcher im Nachhinein nicht mehr vergrößert werden konnten, gab es hierfür leider keine Möglichkeit, diesen Fehler auszubessern.
\subsubsection{Operationsverstärker}
Der Operationsverstärker war zwar als Verstärkerschaltung richtig konfiguriert, allerdings musste die Verstärkerspannung von 3,3V auf 24V angehoben werden, um die 10V zu erreichen. Zusätzlich wurde der Spannungsteiler am Ausgang des OPVs entfernt und der erste Widerstand gegen einen Jumper getauscht.
\subsubsection{RS485 Bias Widerstände}
Die RS485 Widerstände wurden anfänglich nach den empfohlenen Werten in der WSWD Dokumentation dimensioniert. Hier wurde bei einer Versorgungsspannung von 5V ein Busabschlusswiderstand $R_t$ von 120$\Omega$ und zwei Bias-Widerstände $R_b$ von 750$\Omega$ empfohlen (vgl.\cite{WSWD} S.21). Dies sorgte allerdings für eine zu große Differenz der beiden Spannungen und der MAX3485 konnte nicht zwischen HIGH und LOW unterscheiden. Deshalb wurde stattdessen nach der Anleitung des MAX3485 die Differenz zwischen beiden Potenzialen auf 0,2V begrenzt. Hierfür wurde auf die Berechnung in dem von Texas Instruments veröffentlichten Bericht: \glqq{}RS-485 failsafe for an idle bus\grqq{} zurückgegriffen (vgl. \cite{Texas_instruments}). Mithilfe der Formel: 
\begin{equation}
	R_b = (\frac{V_s}{V_{diff }}+1)\times27,8\Omega
\end{equation}
lassen sich die beiden Bias Widerstände für das RS-485 Netzwerk berechnen. Aus den eingesetzten Werten resultiert:
\begin{equation}
	R_b = (\frac{3,3V}{0,2V}+1)\times27,8\Omega = 486,5\Omega
\end{equation}
Der nächstkleinere Widerstand der verfügbaren E24-Reihe wurde mit 470$\Omega$ gewählt. Damit konnte schließlich erfolgreich über RS485 kommuniziert werden.
\subsubsection{FRAM Anschlüsse}
Die SPI-Anschlüsse des FRAM Speichers wurden falsch verbunden. Dabei wurden die \ac{MOSI}- und \ac{MISO}-Leitung vertauscht und der \ac{WP}-Pin auf das Ground-Potenzial gelegt. Dies führte dazu, dass der Speicher nicht adressiert werden konnte und folglich nicht auf gesendete Befehle reagierte. Zuerst wurde der \ac{WP} von dem Ground Potenzial entfernt und schwebend gehalten. Durch das Beobachten der Pegel von MISO-, MOSI- und Clock-Leitung konnte daraufhin erkannt werden, dass diese vertauscht wurden. Die PCB-Spur wurde dementsprechend getrennt und die Pins stattdessen mit Kabeln verbunden.
\subsubsection{Abstandssensor Präzision}
Der Abstandssensor war eine weitere, große Fehlerquelle. Der Abstandsensor hat zwar eine sehr hohe Präzision erreicht, allerdings erst nach einer Aufwärmzeit. Dieser Effekt tritt laut Datenblatt erst unter einer Umgebungstemperatur von -10°C auf (vgl. \cite{OGD580_Datasheet} S.2). Jedoch wurde in mehreren Tests festgestellt, dass bei Stillstand das Display des Sensors mit der Zeit sinkende Werte anzeigt. Um die Ursache dafür zu finden, wurden einige Messreihen durchgeführt. Hierbei wurde der Abstand zum Sensor konstant gehalten und in einem Intervall von 30s der Spannungswert an einem Messpunkt der Platine mit einem Oszilloskop gemessen. Dies wurde für inkrementierende Außerbetriebszeiten wiederholt. Die Messreihe ist in \autoref{fig:Messreihe_Temperatur} dargestellt. Hier ist klar erkennbar, dass erst nach ca. 1400s bzw. 20-25min ein gleichbleibender Spannungswert auslesbar ist. Ebenfalls geht daraus hervor, dass die Präzision mit der Temperatur des Sensors zusammenhängt, da nach kürzeren Außerbetriebszeiten die Differenz sinkt.
\begin{figure}[H]
	\centering
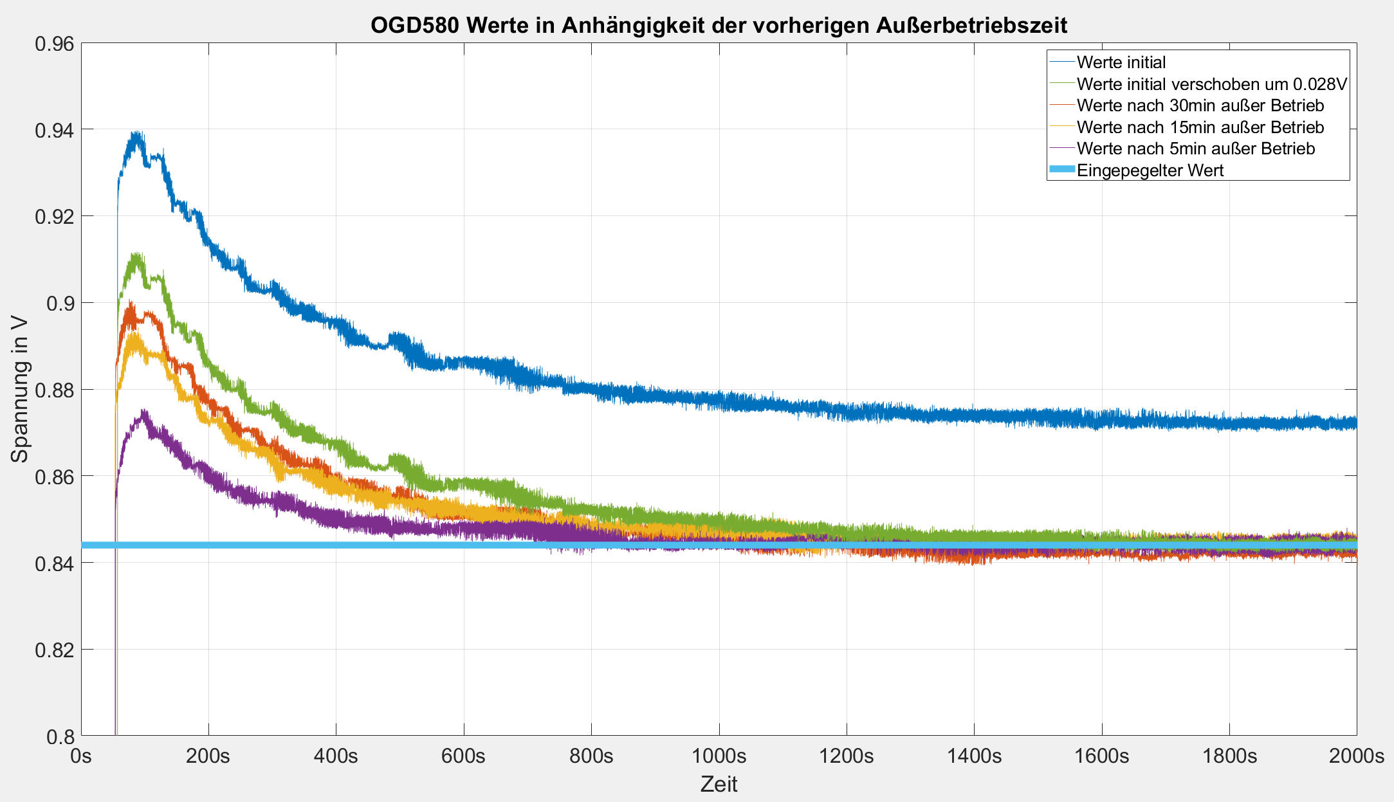
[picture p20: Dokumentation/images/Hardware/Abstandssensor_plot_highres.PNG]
	
	\caption{Messreihen des ausgelesen Spannungswert bei gleichbleibendem Abstand und steigenden Außerbetriebszeiten}
	\label{fig:Messreihe_Temperatur}
\end{figure}

Das Problem blieb allerdings selbst nach einer Aufwärmzeit von 20min. bestehen. Die Abweichungen der ausgelesenen Werte über die Messpunkte von den Werten am Display lagen teilweise bei 25mm. Um die Ursache dieses Problems zu finden, wurden weitere Messreihen aufgenommen. Dabei wurde der Schlitten der Linearführung in 20mm Abständen verschoben. An jedem dieser Punkte wurden folgende Daten notiert:
\begin{itemize}
	\item Abstand zum Sensor, gemessen mit einem Meterstab in mm
	\item Angezeigter Abstand auf dem Display des Sensors in mm
	\item Ausgegebener Strom des IO-Link Konverters gemessen mit einem Multimeter in mA
	\item Spannung am Testpunkt der Platine mit einem Oszilloskop in V
\end{itemize}
Dies wurde in 5 Messreihen wiederholt, um die Reproduzierbarkeit zu verifizieren. Die aufgezeichneten Daten wurden in mm umgerechnet:
\begin{equation}
	L_{Strom} = \frac{L_{max}-L_{min}}{I_{max}-I_{min}}\times(\frac{I_{Position}}{1000}-I_{min}) + L_{min}
\end{equation}
\begin{equation}
	L_{Spannung} = \frac{L_{max}-L_{min}}{I_{max}-I_{min}}\times(\frac{U_{Position}}{153,5\Omega}-I_{min}) + L_{min}
\end{equation}
 und oberhalb der mit dem Meterstab gemessenen Werte geplottet. Eine dieser Messreihen ist in \autoref{fig:Messreihe_Abstand} dargestellt.
\begin{figure}[H]
	\centering
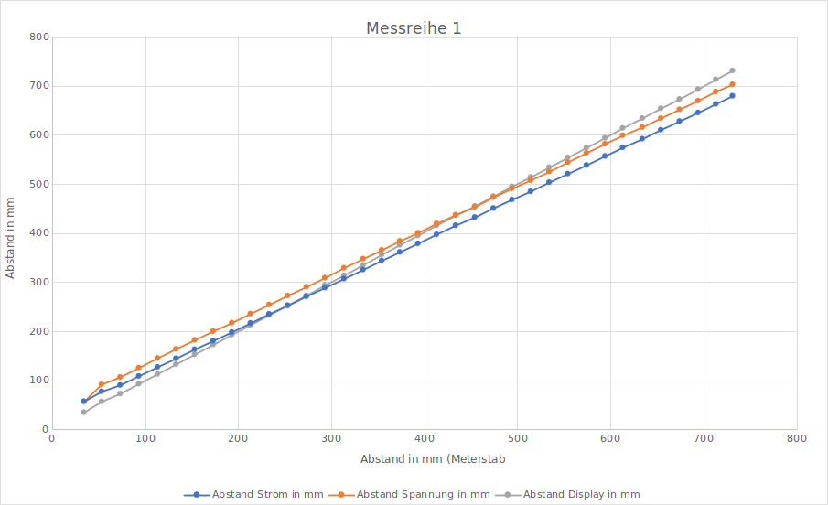
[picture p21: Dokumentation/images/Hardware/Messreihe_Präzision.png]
	
	\caption{Präzision des Abstandssensors anhand verschiedener Messwerte}
	\label{fig:Messreihe_Abstand}
\end{figure}
\noindent Hier ist zu erkennen, dass der auf dem Display abgelesene mit dem gemessenen Abstand übereinstimmt. Allerdings weichen sowohl der Strom- als auch der Spannungswert ab, da die Steigung beider Messreihen nicht gleich zu der des Abstandssensors ist. Dieser ermöglicht die Anpassung der Skalierung. Dabei kann z.B festgelegt werden, ab welchem Messwert das Ausgangssignal 4mA/20mA betragen soll (vgl. \cite{EIO104_Manual}, S.6). Da das Display den korrekten Wert anzeigt, aber ein falscher Strom Wert ausgegeben wird, kann davon ausgegangen werden, dass der Konverter falsch eingestellt ist. Dies konnte im Zuge dieser Arbeit nicht behoben werden, da ein entsprechendes IO-Link Master Gerät nicht verfügbar war.
\subsubsection{Präzision der Analogen Signale}
\label{Mangelnde_Präzision}
Neben den Problemen mit dem Abstandssensor wurden ebenfalls leicht abweichende Werte in den anderen Analogsignalen festgestellt. Beginnend mit den Stromsignalen, kann der ausgelesene Wert mit der Präzision des Widerstandes zusammenhängen, da diese mit 1\% Genauigkeit immer noch große Temperaturabweichungen aufweisen können. Die schlechten Kontakte tragen ebenfalls zur Ungenauigkeit bei. Speziell beim Stromsensor kann auch hier die Positionierung eine Fehlerquelle sein, da die verbundenen Spuren für optimale Präzision im 45° Winkel zu den Sensorpins stehen sollten (vgl. \cite{Stromsensor_texas}, S.37). Um die Präzision zu verbessern, können zusätzlich zu den Widerständen Ferrite eingesetzt werden. Diese verhalten sich ähnlich wie Spulen und filtern hochfrequente Signale. In Kombination mit den bereits verwendeten Kondensatoren würden diese einen LC-Filter darstellen und einen Bandpass erzeugen, der zusätzlich die Signalqualität verbessert.\\

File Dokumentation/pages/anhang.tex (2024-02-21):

\appendix
\section{Schaltpläne}
\label{sec:Schaltplan}
\subsection{Schaltplan Übersicht}
\begin{figure}[H]
	\centering
	
	\caption{Schaltplan Übersicht}
	\label{fig:Schaltplanuebersicht}
\end{figure}
\subsection{Schaltplan STM32F439 Gruppe}
\begin{figure}[H]
	\centering
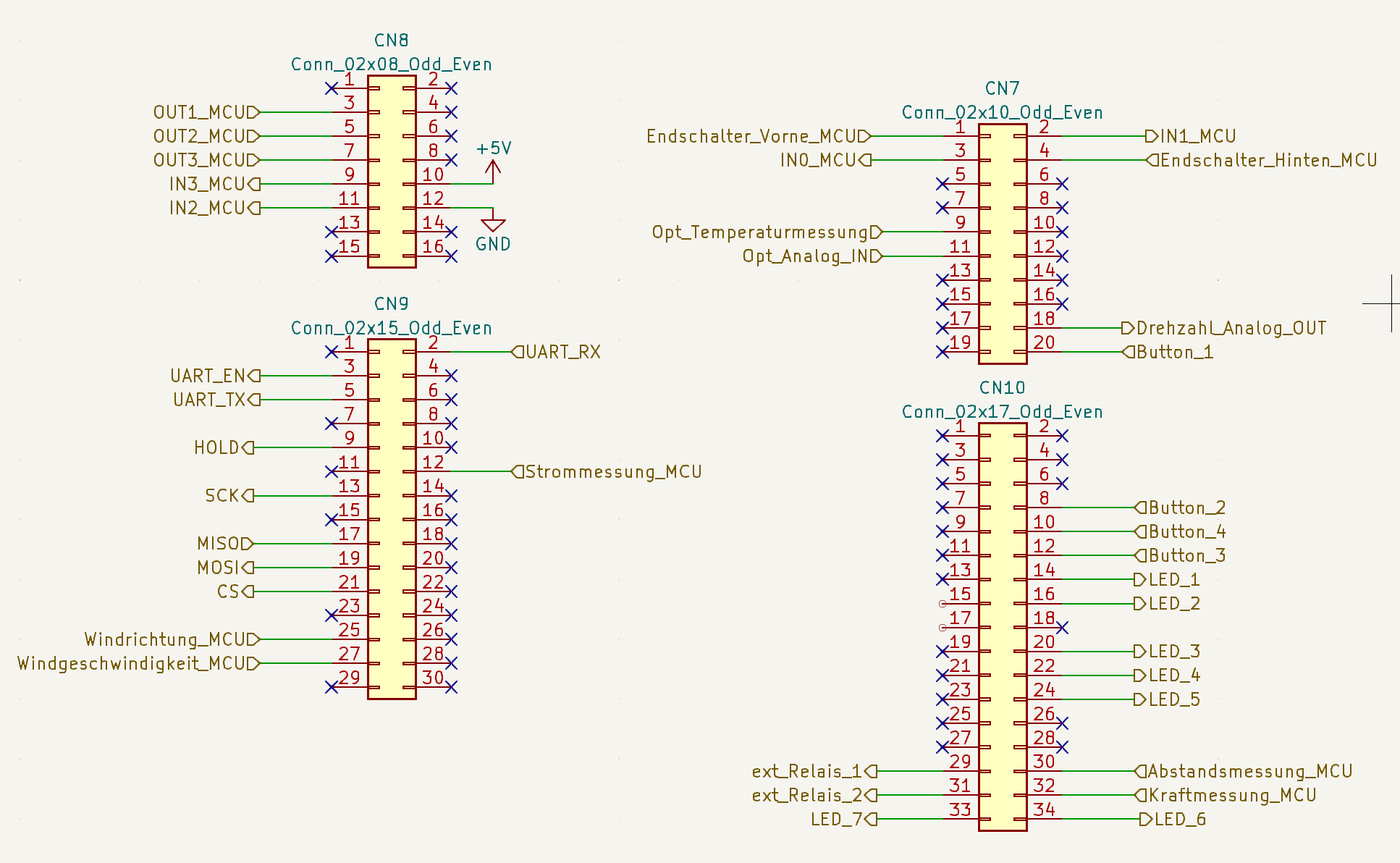
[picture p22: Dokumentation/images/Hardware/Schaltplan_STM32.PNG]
	
	\caption{Schaltplan der STM32F439 Gruppe}
	\label{fig:STM32Gruppe}
\end{figure}
\subsection{Schaltplan Buttons und LED Gruppe}
\begin{figure}[H]
	\centering
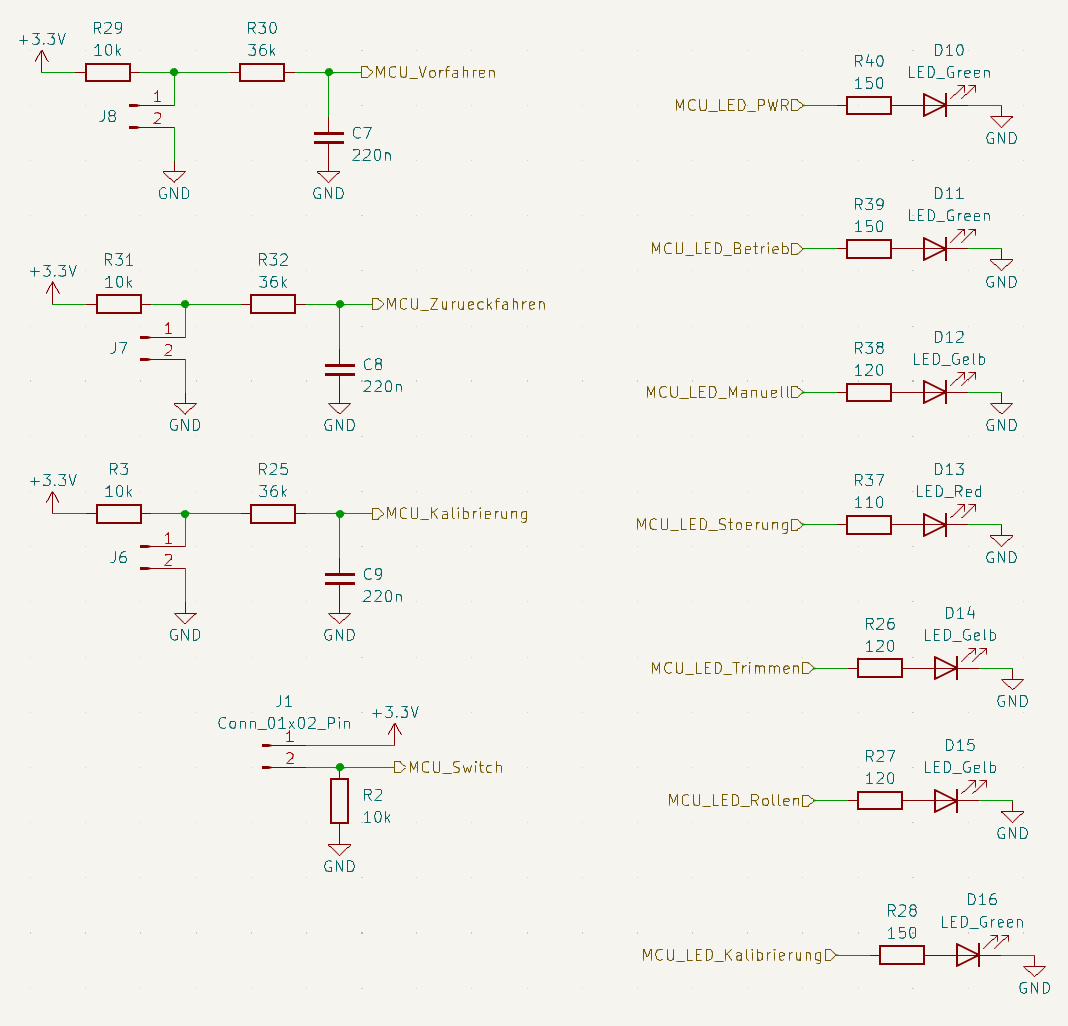
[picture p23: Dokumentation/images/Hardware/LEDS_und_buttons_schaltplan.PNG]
	
	\caption{Schaltplan der Buttons und LED Gruppe}
	\label{fig:ButtonGruppe}
\end{figure}
\subsection{Schaltplan Sensoren Gruppe}
\begin{figure}[H]
	\centering
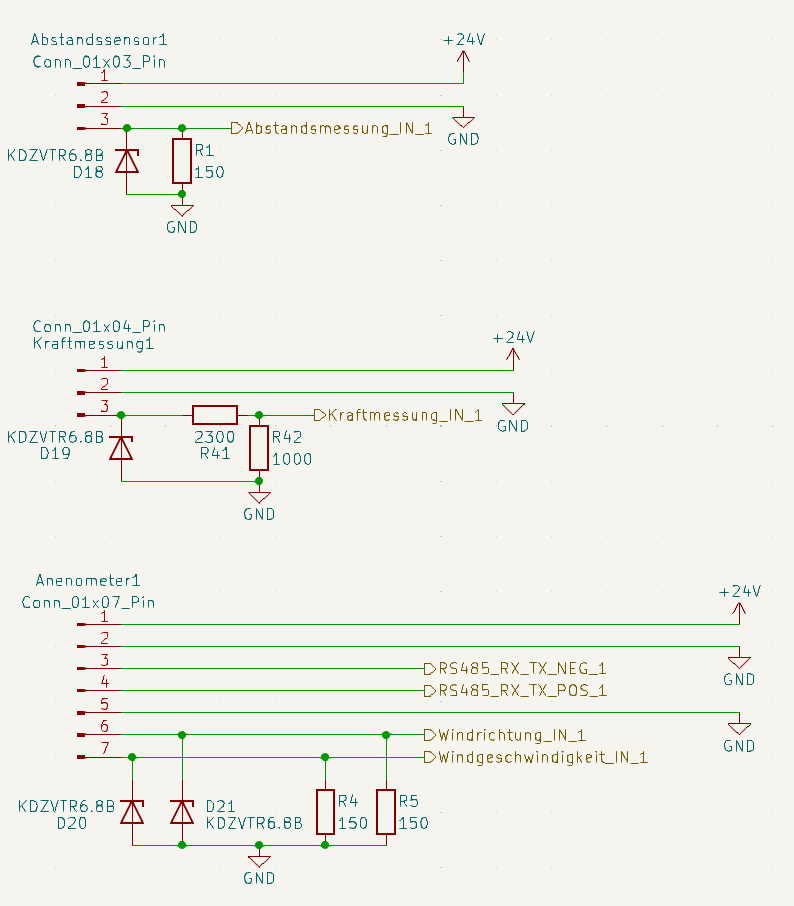
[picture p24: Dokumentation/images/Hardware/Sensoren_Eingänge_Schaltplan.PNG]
	
	\caption{Schaltplan der Sensoren Gruppe}
	\label{fig:SensorenGruppe}
\end{figure}
\subsection{Schaltplan Motor Gruppe}
\begin{figure}[H]
	\centering
	
	\caption{Schaltplan der Motor Gruppe}
	\label{fig:MotorGruppe}
\end{figure}
\subsection{Schaltplan Endschalter Gruppe}
\begin{figure}[H]
	\centering
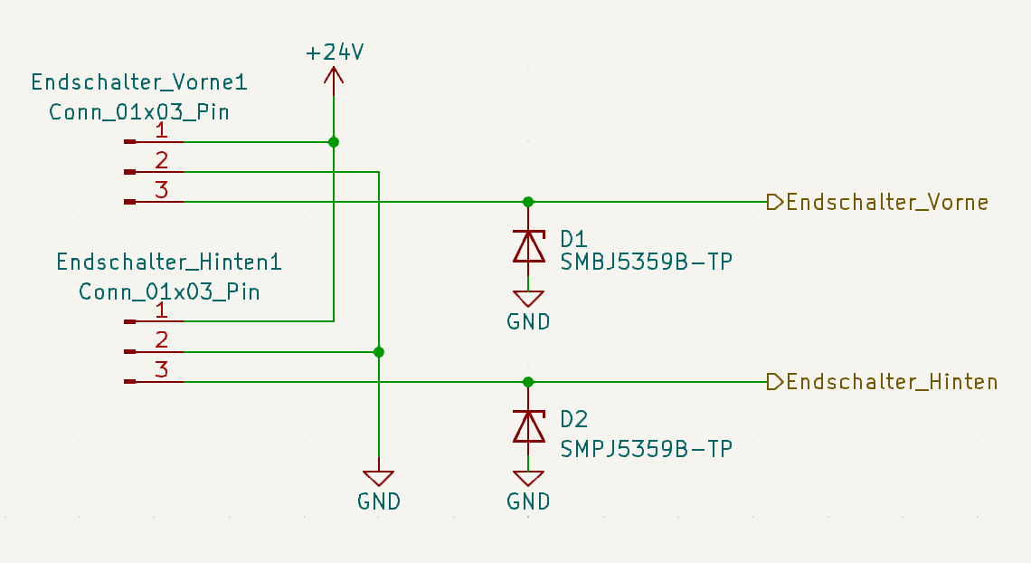
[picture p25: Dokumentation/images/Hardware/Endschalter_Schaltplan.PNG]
	
	\caption{Schaltplan der Endschalter Gruppe}
	\label{fig:EndschalterGruppe}
\end{figure}
\section{Bauteilliste}
\label{sec:Bauteilliste}
\begin{table}[H]
	\centering
	\resizebox{\textwidth}{!}{%
		\begin{tabular}{|l|l|l|}
			\hline
			\textbf{Bauteilbezeichnung} & \textbf{Bauteilart} & \textbf{Anzahl} \\ \hline
			Schurter TASTER 1104 GN & Button, Grün & 1 \\ \hline
			Schurter TASTER 1104 SW & Button, Schwarz & 2 \\ \hline
			LM3940IMP-3.3/NOPBCT-ND & Festspannungsregler & 1 \\ \hline
			FM25L16B-GTRCT-ND & F-RAM & 1 \\ \hline
			C1Q 4 & Fuse 1206, 4A & 1 \\ \hline
			3413.0223.22 & Fuse 1206, 5A & 1 \\ \hline
			RP1465 & Gehäuse & 1 \\ \hline
			R-78E5.0-0.5 & DC/DC Wandler & 1 \\ \hline
			Phoenix Contact 1984617 & Schraubterminal 2 Fach 3.5mm & 2 \\ \hline
			OSTVN02A150 & Schraubterminal 2 Fach 2.54mm & 3 \\ \hline
			OSTVN03A150 & Schraubterminal 3 Fach 2.54mm & 4 \\ \hline
			TE Connectivity 282834-7 & Schraubterminal 7 Fach  2.54mm & 1 \\ \hline
			OSTVN10A150 & Schraubterminal 10 Fach 2.54mm & 1 \\ \hline
			LM2904QS-13DICT-ND & Operationsverstärker & 1 \\ \hline
			MAX3485CSA+CT-ND & RS-485 Converter & 1 \\ \hline
			TMCS1101A3BQDRQ1CT-ND & Stromsensor & 1 \\ \hline
			LTST-C150GKT & SMD LED Grün & 3 \\ \hline
			LTST-C150KSKT & SMD LED Gelb & 3 \\ \hline
			LTST-C230KRKT & SMD LED Rot & 1 \\ \hline
			LTST-C230KFKT & SMD LED Orange & 1 \\ \hline
			LTV-817S & Optokoppler & 9 \\ \hline
			G6S-2F 24DC & Relais, 24V & 2 \\ \hline
			KDZVTR24BCT-ND & Zenerdiode, 24V & 9 \\ \hline
			Schurter FRONTSATZ & Button, Montagesatz & 3 \\ \hline
			C6000ALBB & Schalter & 1 \\ \hline
			C6000ALBB-1229W & Schalter, gekennzeichnet & 1 \\ \hline
			SL 2X10G SMD2,54 & Pin-Header, SMD & 1 \\ \hline
			SL 2X50G 2,54 & Pin-Header & 1 \\ \hline
			MEN 1216.1001 & LED-Lichtleiter & 8 \\ \hline
			KDZVTR6.8B & Zenerdiode, 6.8V & 4 \\ \hline
			IPG-2227 & Kabelverschraubung 3mm-6mm & 4 \\ \hline
			IPG-222135 & Kabelverschraubung 6mm-12mm & 4 \\ \hline
		\end{tabular}%
	}
	\caption{Bauteilliste Teil 1}
	\label{tab:Verwendeten Bauteile}
\end{table}
\begin{table}[H]
	\centering
	\begin{tabular}{|l|l|}
		\hline
		\textbf{Widerstände SMD1206} & \textbf{Anzahl} \\ \hline
		150$\Omega$ & 7 \\ \hline
		10k$\Omega$ & 5 \\ \hline
		120$\Omega$ & 4 \\ \hline
		750$\Omega$ & 2 \\ \hline
		240$\Omega$ & 1 \\ \hline
		700$\Omega$ & 6 \\ \hline
		11k$\Omega$ & 6 \\ \hline
		2,2k$\Omega$ & 3 \\ \hline
		6,8k$\Omega$ & 3 \\ \hline
		36k$\Omega$ & 3 \\ \hline
		110$\Omega$ & 1 \\ \hline
		2,3k$\Omega$ & 1 \\ \hline
		1k$\Omega$ & 1 \\ \hline
		\textbf{Kondensatoren SMD1206} &  \\ \hline
		22$\mu$F & 1 \\ \hline
		22nF & 6 \\ \hline
		220nF & 3 \\ \hline
		33$\mu$F & 1 \\ \hline
		0.47$\mu$F & 1 \\ \hline
	\end{tabular}
	\caption{Bauteilliste Teil 2}
	\label{tab:Bauteile2}
\end{table}
\newpage
\section{Valide URL und JSON Formate}
\label{sec:REST}
\subsection{GET-Anfragen}
\subsubsection{GET /data}
\begin{lstlisting}[language=XML, caption={GET-Request 1}]
{
	"error": <(int) error_code>,
	"operating_mode": <(int) 0/1 [manual/automatic]>,
	"localized": <(boolean)>,
	"sail_pos": <(int) pitch/roll [+/- 0...100 %]>,
	"wind": {
		"speed": <(int) speed[m/s]>,
		"direction": <(int) direction[degree]>
	},
	"current": <(int) current[mA]>
}
\end{lstlisting}
\subsubsection{GET /data/status}
\begin{lstlisting}[language=XML, caption={GET-Request 2}]
	{
		"error": <(int) error_code>,
		"operating_mode": <(int) 0/1 [manual/automatic]>,
		"localized": <(boolean)>,
	}
\end{lstlisting}
\subsubsection{GET /data/adjustment}
\begin{lstlisting}[language=XML, caption={GET-Request 3}]
	{
		"sail_pos": <(int) pitch/roll [+/- 0...100 %]>
	}
\end{lstlisting}
\newpage
\subsubsection{GET /data/sensors}
\begin{lstlisting}[language=XML, caption={GET-Request 4}]
	{
		"wind": {
			"speed": <(int) speed[m/s]>,
			"direction": <(int) direction[degree]>
		},
		"current": <(int) current[mA]>
	}
\end{lstlisting}
\subsubsection{GET /data/settings}
\begin{lstlisting}[language=XML, caption={GET-Request 5}]
	{
		"max_rpm": <(int) 400 - 2000>,
		"max_distance_error": <(int) 5 - 50>
	}
\end{lstlisting}

\subsection{PUT-Anfragen}
\subsubsection{PUT /data/status/error}
\begin{lstlisting}[language=XML, caption={PUT-Request 1}]
	{
		"error": <(int) error_code>,
	}
\end{lstlisting}
\newpage
\subsubsection{PUT /data/adjustment}
\begin{lstlisting}[language=XML, caption={PUT-Request 2}]
	{
		"sail_pos": <(int) pitch/roll [+/- 0...100 %]>
	}
\end{lstlisting}
\subsubsection{PUT /data/status/operating\_mode}
\begin{lstlisting}[language=XML, caption={PUT-Request 3}]
	{
		"operating_mode": <(int) 0/1 [manual/automatic]>
	}
\end{lstlisting}
\subsubsection{PUT /data/settings}
\begin{lstlisting}[language=XML, caption={PUT-Request 4}]
	{
		"max_rpm": <(int) 400 - 2000>,
		"max_distance_error": <(int) 5 - 50>
	}
\end{lstlisting}

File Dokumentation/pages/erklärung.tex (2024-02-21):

\nonumsection{Eidesstattliche Erklärung}
\thispagestyle{empty}
\vspace*{2em}

Wir versichern hiermit, dass wir dieses Bachelorprojekt mit dem Thema:
\begin{center}
	\vspace{2em}
	\bf\large\myTopic\rm
	\vspace{2em}
\end{center}
\noindent selbstständig verfasst und keine anderen als die angegebenen Quellen und Hilfsmittel benutzt haben.

\vspace{4em}

\noindent \myEndPlace, \myEndDate
\vspace{4em}

\noindent\rule{6cm}{0.4pt}\hfill\rule{6cm}{0.4pt}\\
\myAutor\hfill\myAutorTwo

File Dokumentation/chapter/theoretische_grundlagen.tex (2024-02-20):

\newpage
\section{Grundlagen zur Segeleinstellung}\label{sec:principles}
In diesem Kapitel wird grob auf die Bedeutung und Funktionsweise der Segelsteuerung eingegangen. Nachfolgende Informationen basieren auf dem Wissensstand der Vorgruppe, in deren Arbeit auf genauere Details zu dieser Thematik verwiesen wird. Eine Skizze, die daraus entnommen wurde, veranschaulicht den Sachverhalt des Segelanstellwinkels:
\begin{figure}[H]
	\centering
	
	\caption{Segeltheorie: Scheinbarer Wind und Anstellwinkel}
	\label{fig:sailPitch}
\end{figure}
\noindent
Bei einem Segelboot beeinflusst der Fahrtwind den wahren Wind (hier \textit{Anströmung}) zu einem scheinbaren Wind, der effektiv in das Segel bläst. Ähnlich verhält es sich bei einem in diesem Fall segelartigen Rotorblatt, dass den Wind durch die erzeugte Rotation ablenkt. Verändert sich die Anströmungsgeschwindigkeit, muss der Anstellwinkel des Segels entsprechend angepasst werden, sodass der resultierende scheinbare Wind möglichst effizient vom Segel aufgenommen und in Rotation umgewandelt wird. So existiert zu jeder Windgeschwindigkeit ein optimaler Anstellwinkel. Diese Anpassung wird auch als Trimmen des Segels bezeichnet.\\

\noindent
Wie bereits in der Einleitung erwähnt soll bei einer Windgeschwindigkeit von 14 m/s eine Leistung von 5 kW erzeugt werden. Damit diese auch bei stärkerem Wind konstant abrufbar ist, soll die Segelfläche durch Einrollen verkleinert werden. \autoref{fig:powerCurve} zeigt die erwartete Leistungskurve in Abhängigkeit der Windstärke bei gezielter Trimmung und Rollung der Segel:
\begin{figure}[H]
	\centering
	
	\caption{SAILWIND Leistungskurve nach Prof. Schwechten}
	\label{fig:powerCurve}
\end{figure}
\noindent
Die Seilführung der Segel (siehe \autoref{fig:sailWindMill}) ermöglicht dabei einen fließenden Übergang zwischen Rollung und Trimmung durch eine gemeinsame Zugbewegung aller Seile parallel zur Rotorwelle, die mithilfe der Linearführung ausgeführt werden soll. Bei einer Einschaltgeschwindigkeit von 1 bis 2 m/s sollen die Segel vollständig getrimmt und ausgerollt sein. Bis zur Nenngeschwindigkeit von 14 m/s befindet sich das System im Teillastbereich, in dem der Anstellwinkel schrittweise reduziert werden soll, um stets die optimale Leistung herauszuholen. Mit weiterem Anstieg der Windgeschwindigkeit beginnt der Volllastbereich, in dem die Segel immer weiter eingerollt werden, um die Spitzenleistung von 5 kW zu erhalten. Ab einem kritischen Wert von ca. 18 m/s soll ein Abregelungsprozess durchgeführt werden.

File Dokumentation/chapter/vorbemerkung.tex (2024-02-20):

\nonumsection{Vorbemerkung}
In der folgenden Arbeit wird aus Gründen der besseren Lesbarkeit ausschließlich die männliche Form verwendet. Sie bezieht sich auf alle Geschlechter gleichermaßen.

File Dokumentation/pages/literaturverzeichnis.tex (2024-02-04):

\nonumcontent{Literaturverzeichnis}
\printbibliography

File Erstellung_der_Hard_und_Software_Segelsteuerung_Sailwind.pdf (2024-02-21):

# Erstellung der Hard- und Software zur

# Steuerung der Segel im Sailwind 4.0

# Projekt

Projektarbeit

An der Fakultät Elektro- und Informationstechnik

vorgelegt von

Benedikt Horn und Nico Finkbeiner

Matrikelnummer: 300889 und 298837

Hochschule Konstanz fur Technik, Wirtschaft und Gestaltung ¨

Hochschulbetreuer:
Prof. Dr. Boris Böck
Prof. Dr. Dieter Schwechten

Konstanz den 21. Februar 2024

## Eidesstattliche Erklärung

Wir versichern hiermit, dass wir dieses Bachelorprojekt mit dem Thema:

### Erstellung der Hard- und Software zur Steuerung der

### Segel im Sailwind 4.0 Projekt

selbstständig verfasst und keine anderen als die angegebenen Quellen und Hilfsmittel benutzt haben.

Konstanz, 21.02.2024

Nico Finkbeiner | Benedikt Horn

Inhaltsverzeichnis | ii

## Inhaltsverzeichnis

Eidesstattliche Erklärung | i
Abkurzungsverzeichnis ¨ | vi
Abbildungsverzeichnis | viii
Quellcodeverzeichnis | x
Vorbemerkung | 1
1 Einleitung | 2
2 Grundlagen zur Segeleinstellung | 4
3 Hardware | 6

Inhaltsverzeichnis | iii
4 Software | 32

Inhaltsverzeichnis | iv
4.3.5 | Fehlerbehandlung | 52
4.4 Windmessung mit dem Anemometer | 53
4.5 Representational State Transfer (REST) Interface | 54
4.6 Weboberfläche | 56
4.6.1 | Funktionalität | 56
4.6.2 | Webseiten | 56
4.6.3 | Umsetzung | 57
5 Fazit und Ausblick | 59
Literaturverzeichnis | xi
A Schaltpläne | xiii
A.1 Schaltplan Ubersicht ¨ | | xiii
A.2 Schaltplan STM32F439 Gruppe | xiv
A.3 Schaltplan Buttons und LED Gruppe | xv
A.4 Schaltplan Sensoren Gruppe | xvi
A.5 Schaltplan Motor Gruppe | xvii
A.6 Schaltplan Endschalter Gruppe | xviii
B Bauteilliste | xx
C Valide URL und JSON Formate | xxii
C.1 GET-Anfragen | xxii
C.1.1 GET /data | xxii
C.1.2 GET /data/status | xxii
C.1.3 GET /data/adjustment | xxii
C.1.4 GET /data/sensors | xxiii
C.1.5 GET /data/settings | xxiii
C.2 PUT-Anfragen | xxiii
C.2.1 PUT /data/status/error | xxiii
C.2.2 PUT /data/adjustment | xxiv

Inhaltsverzeichnis | v

Inhaltsverzeichnis | vi

## Abkurzungsverzeichnis ¨

API Application Programming Interface

BLDC Brushless DC

CGI Common Gateway Interface

DAC Digital Analog Converter

DC Direct Current

DHCP Dynamic Host Configuration Protocol

FRAM Ferroelectric Random Access Memory

GPIO General-Purpose Input/Output

HTTP Hypertext Transfer Protocol

HTML Hypertext Markup Language

IP Internet Protocol

JSON Java Script Object Notation

LED Light Emitting Diode

LWIP Lightweight IP

MSB Most significant Bit

MISO Master In Slave Out

MOSI Master Out Slave In

NMEA National Marine Electronics Association

PCB Printed Circuit Board

REST Representational State Transfer

SMD Surface-Mount Device

SPI | Serial Peripheral Interface
SSI | Server Side Includes

Inhaltsverzeichnis | vii
TCP | Transmission Control Protocol

UART Universal Asynchronous Receiver/Transmitter

URI | Uniform Resource Identifier
URL | Uniform Resource Locator
WP | Write Protect

WREN Write Enable

Abbildungsverzeichnis | viii

## Abbildungsverzeichnis

1 | Segelwindmuhle auf der griechischen Insel Kos ¨ | | | 2
2 | Segeltheorie: Scheinbarer Wind und Anstellwinkel | | 4
3 | SAILWIND Leistungskurve nach Prof. Schwechten | | 5
4 | Simplifiziertes 3D Modell der Linerafuhrung ¨ | | | 6
5 | Blockschaltbild der benötigten Ein- und Ausgänge der Platine . . . 12
6 | Schaltplan des Texas Instruments TMCS1101 Hall Stromsensor (vgl.
[7], S.24) | 16
7 | 3D Modell der Platine innerhalb des Gehäuses | 18
8 | Bedienoberfläche der Segel Steuerung | 19
9 | Gesamtschaltplan der Platine | 20
10 | Schaltplan der Motorgruppe | 22
11 | Beispielhafte Schaltung eines Optokopplers | 23
12 | Schaltplan des analogen Eingangs des Abstandsensors | 24
13 | RC-Filter fur einen am Geh ¨ | äuse angebrachten Knopf | 25
14 | 3D Ansicht des fertigen PCBs | 26
15 | Messreihen des ausgelesen Spannungswert bei gleichbleibendem Ab-
stand und steigenden Außerbetriebszeiten | 29
16 | Präzision des Abstandssensors anhand verschiedener Messwerte . . 31
17 | Software Modulstruktur | 33
18 | Drehzahlrampe: Beschleunigen und Bremsen | 40
19 | Kalibrierungsprozess | 42
20 | Rollung und Trimmung an der Linearfuhrung ¨ | | 43
21 | Optimierung der Steuerbefehle | 47
22 | Aufbau eines NMEA Telegramm (vgl.[9], S.61) | 53
23 | Index Seite des Webservers | 57
24 | Schaltplan Ubersicht ¨ | | xiii
25 | Schaltplan der STM32F439 Gruppe | xiv
26 | Schaltplan der Buttons und LED Gruppe | xv
27 | Schaltplan der Sensoren Gruppe | xvi

Abbildungsverzeichnis | ix
28 | Schaltplan der Motor Gruppe | xvii
29 | Schaltplan der Endschalter Gruppe | xviii

Quellcodeverzeichnis | x

## Quellcodeverzeichnis

1 | Struktur fur digitale Pins ¨ | | 34
2 | Einlesen eines digitalen Pin-Zustands | 35
3 | Detektion einer Flanke | 35
4 | Struktur fur analoge Sensoren ¨ | | 36
5 | Konvertierung des rohen Analogwerts | 36
6 | Struktur des Motors | 38
7 | Einstellung der Motorfunktionen | 39
8 | Berechnung der Zielposition | 44
9 | Positionsberechnung aus dem Pulssignal des Motors | 45
10 | Speicherformat der Positionsdaten | 49
11 | FRAM Speichervorgang | 50
12 | Auslesen der Positionsdaten aus dem FRAM-Puffer | 51
13 | Empfangen einer Nachricht vom WSWD | 54
14 | GET /data/adjustment Antwort Paket | 55
15 | GET /data/adjustment Antwort Paket | 58
16 | GET-Request 1 | xxii
17 | GET-Request 2 | xxii
18 | GET-Request 3 | xxii
19 | GET-Request 4 | xxiii
20 | GET-Request 5 | xxiii
21 | PUT-Request 1 | xxiii
22 | PUT-Request 2 | xxiv
23 | PUT-Request 3 | xxiv
24 | PUT-Request 4 | xxiv

Quellcodeverzeichnis | 1

## Vorbemerkung

In der folgenden Arbeit wird aus Grunden der besseren Lesbarkeit ausschließlich ¨ die männliche Form verwendet. Sie bezieht sich auf alle Geschlechter gleichermaßen.

1 Einleitung | 2

## 1 Einleitung

In der Durchfuhrung der globalen Energiewende spielt die Windkraft eine große ¨ Rolle. Jedoch treffen Projekte zum Bau großer Anlagen immer wieder auf Widerstand der Anwohner aufgrund der Verunstaltung der Landschaft. Das SAILWIND Projekt soll dem entgegen kommen und entstand aus der Motivation heraus, kleine, griechische Segelwindmuhlen, zu renovieren. ¨


Abbildung 1: Segelwindmuhle auf der griechischen Insel Kos [ ¨ | 1]

Vor 3000 Jahren dienten diese noch zum Antrieb von Wasserrädern fur den Ge- ¨ treidebau. Mit der Umsetzung des Projekts sollen nun zahlreiche dieser heute ungenutzten Bauwerke zur Erzeugung erneuerbarer Energie umfunktioniert werden. Dabei soll die Optik der Muhlen ¨ äußerlich möglichst unverändert bleiben. Lediglich die Segel werden erneuert und die Welle an einen Generator gekoppelt, der bei einer Windstärke von 14 m/s eine Spitzenleistung von 5 kW abgeben soll. Diese reicht aus, um z.B. ein ganzes Restaurant zu versorgen. [2] Um die Windmuhle ¨

1 Einleitung | 3

effizient zu betreiben, soll eine voll automatisierte Steuerung integriert werden, welche die Segel der Windstärke und -Richtung entsprechend einstellt. Die Ein-
stellung der Segel geschieht dabei uber die Verbindung einer Seilf ¨ | uhrung (wie in ¨
Abbildung 1 zu sehen) mit einer motorisierten Linearfuhrung. ¨
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

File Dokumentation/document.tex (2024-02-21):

\begin{document}
	\pagestyle{fancy}
	\addtocontents{toc}{\vspace{0.125 cm}}
	\fancyhead[L]{\nouppercase{\leftmark}}

    \include{titelblatt}
    \onehalfspacing

    \frontmatter %-------------------------------------------------

    \include{pages/erklärung}
    \include{pages/inhaltsverzeichnis}
    \include{pages/abkürzungsverszeichnis}
    \include{pages/abbildungsverzeichnis}
    \include{pages/codelisting}
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

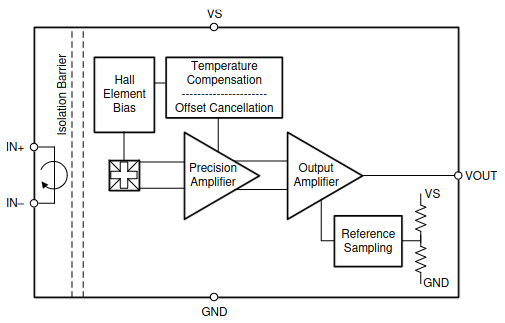
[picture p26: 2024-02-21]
Dokumentation/images/Hardware/Schaltplan_Stromsensor.png

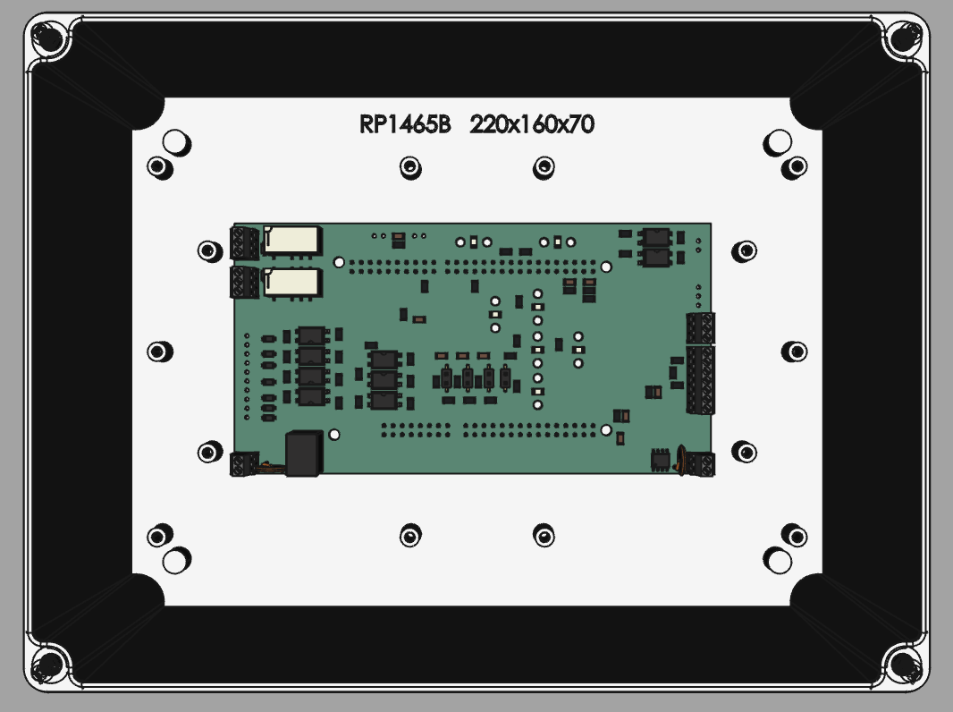
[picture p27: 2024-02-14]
Dokumentation/images/Hardware/Platine_in_gehauese_kein_wireframe.PNG

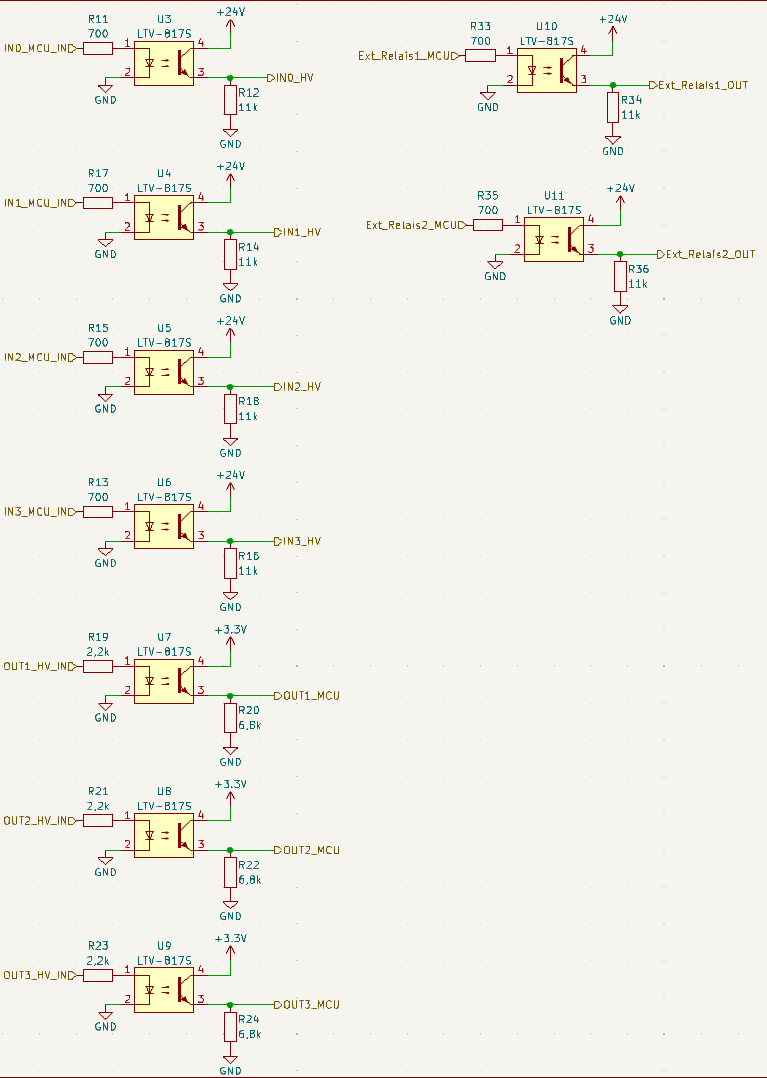
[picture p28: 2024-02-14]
Dokumentation/images/Hardware/Optokoppler_Schaltplan.PNG

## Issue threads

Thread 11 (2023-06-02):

implement motor calibration

BeneHTWG, 2023-06-02:
- [x] statemachine for calibrate button
- [x] statemachine for setting endpoints
- [x] function to calculate distance in mm from pulse count and to set endpoints
- [x] function to detect endpoints
- [x] function to set center position
- [ ] test rpm callback function to measure motor pulse output signal

BeneHTWG, 2023-06-02:
Idea:
1) in manual operation mode, the calibration button shall be pressed to call the "motor_button_calibrate_state_machine()"
    function within its eventhandler
2) this state machine has 4 states, wich are saved/updated in the main struct object "motor.calibration.state":
       0. motor_calibration_state_0_init
       1. motor_calibration_state_1_save_endpoints
       2. motor_calibration_state_2_set_center_pos (see p. 8))
       3. motor_calibration_state_3_done
3) after pressing the button for the first time, the state changes to "state_1"
4) this causes the start of another state machine within "motor_calibrate_state_machine_set_endpoints()", that shall be called in
    the main loop to handle the movement to the endpoints, which has the following 3 states:
       0. motor_set_endpoints_state_0_init
       1. motor_set_endpoints_state_1_move_to_end_pos_vorne
       2. motor_set_endpoints_state_2_move_to_end_pos_hinten
5) in state_0, the motor is started in direction to the front endpoint and state is set to state_1
6) in state_1, the sensor for the front endpoint is read in and if it is reached, the direction of the motor movement is changed
    towards the back endpoint and state is changed to state_2. Additionally, the "motor.calibration.start_pulse_count" flag is set
    True, which causes the motor.calibration.current_pos_pulse_count to be inc-/decremented (depending on the motor
    direction) in every iteration within the "motor_callback_get_rpm()" function, which is frequently called by a timer.
    With the pulse count, the current position can be converted to a distance in mm as soon as the motor moved to both
    endpoints once.
7) in state_2, the sensor of the back endpoint is read in and if it is reached, the endpoints positions are calculated and
    normalized to have the actual center at 0 mm. Also the direction of the motor is changed again, to move towards the center.
    Finally, the state of the top state machine is set to state_2_set_center_pos.
8) if the calibration button is pressed a second time and the state is state_2_set_center_pos, the function
    "_motor_calibrate_set_center()" is called, where the center position is saved and the motor is stopped. After that the state is
    set to state_3_done and the calibration process is over.

BeneHTWG, 2023-06-04:
new functionality:
- manual moving of the motor is now only allowed before and after calibration process
- the operating mode can only be switched to automatic, if the calibration process is over, hence the center position is set.
- when the center position is set, the respective LED is switched on
- after the calibration process, the center pos can still be adjusted by using the move left/right buttons
- doing that, the center pos LED is switched off, but the last center position is still saved
- when the desired position is manually reached, the calibration button shall be pressed again to save the new center position,
  which turns the LED on again
- after that, the operating mode can be switched to automatic
- when switching to automatic, the center pos LED is switched on, if it was off due to moving the motor manually without
  saving a new center posititon (continue with previous position)

BeneHTWG, 2023-06-05:
new functionality (66c657bdf4e6cce019a4344e2a7eb098e7babb2d):
- added motor moving state member to motor struct (aus, rechts, links), which is set in the start_ / stop_moving functions
- rpm callback function counts pulse up or down depending on moving state
- rpm measurement is now started, after the first end position is reached within the calibration process

Closed 2023-06-18.

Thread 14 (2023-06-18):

linear guide api

BeneHTWG, 2023-06-18:
- [x] new source file to treat functionality of the whole linear guide system
- [x] move calibration functions and end-switches from motor api to linear guide api
- [x] complete documentation of all functions in the project
- [x] change calibration process:
      - after reaching both end positions, the motor shall drive to the calculated center and stop there
      - afterwards the center position can be adjusted manually and finally confirmed/saved by pressing the calibration button
- [ ] test stop condition (pos == 0 mm) when approaching the center pos in calibration process
- [x] make one state machine with two separate functions (for button event and main loop)
- [x] test if motor can change direction immediately after reaching end switch, or if it must be stopped in between for a
       short time
- [x] add sensors as members of linear guide struct and write init functions for them

Closed 2023-08-14.

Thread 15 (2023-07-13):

Test Branch

BeneHTWG, 2023-07-13:
Checklist for successfull tests

- [ ] FRAM -> read/write
- [ ] Motor/digitalInputs -> set motor function
- [ ] Motor/digitalOutput/rpmmeasurement
- [ ] Motor/digitalOutput/direction
- [ ] Motor/digitalOutput/Error
- [ ] Motor/analogInput -> rpm setting
- [ ] EndSwitch -> hardware controlled motor stop
- [ ] EndSwitch -> software controlled
- [ ] LED Bar -> all LEDs work properly
- [ ] Buttons -> all Buttons work properly
- [ ] Current sensor
- [ ] Distance sensor
- [ ] Force sensor
- [ ] UART Interface
- [ ] Web server

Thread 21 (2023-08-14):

Fix Pin assignments

derfinke, 2023-08-14:

Closed 2023-08-14.

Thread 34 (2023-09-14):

REST Controllino Interface

BeneHTWG, 2023-09-14:
### Requests from Controllino:
**GET Request:**

	"data"
	- pld:

		{
			"error": <(int) error_code>,
			"operating_mode": <(int) 0/1 [manual/automatic]>,
			"localized": <(boolean)>,
			"actual_adjustment": {
				"mode": <(int) 0/1 [rollung/trimmung]>,
				"rollung": <(int) rollung[%]>,
				"trimmung": <(int) trimmung[%]>,
				"speed": <(int) speed[mm/s]>
			},
			"wind": {
				"speed": <(int) speed[m/s]>,
				"direction": <(int) direction[degree]>
			},
			"current": <(int) current[mA]>
		}

**PUT** Request:

	"error"
	- pld:
		<(int) error_code>

	"set_adjustment"
	- pld:
		{
			"mode": <(int) 0/1 [rollung/trimmung]>,
			"rollung"/"trimmung": <(int) rollung/trimmung[%]>
		}

	"set_operating_mode"
	- pld:
		<(int) 0/1 [manual/automatic]>

### possible Errorcodes:

**from** stm:
  - 0: normal -> continue
  - 1: motor error -> emergency shutdown
  - 2: high current -> emergency shutdown

**from controllino:**
  - 0: normal -> continue
  - 3: strong wind -> emergency shutdown

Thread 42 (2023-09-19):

add speed ramps to motor movements

BeneHTWG, 2023-09-19:

BeneHTWG, 2023-09-20:
bug fix in #56

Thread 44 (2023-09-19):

change LED_trimmen and LED_rollen pin

derfinke, 2023-09-19:
Currently LEDs are not set correctly and new pins have to be assigned respectively

BeneHTWG, 2023-09-25:
LEDs are now switched

Closed 2023-09-25.

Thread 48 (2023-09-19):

Use measured distance from distance sensor to determine accuracy

derfinke, 2023-09-19:

BeneHTWG, 2023-09-27:
fixed in #62: now distance is converted properly to relative distance by capturing the absolute start point when hitting the front endswitch
also when a delta of 10mm is reacched, a direct partial recover is triggered in the Localization

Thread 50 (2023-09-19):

Actually use last saved position in FRAM

derfinke, 2023-09-19:
currently the last saved center position is ignored or used incorrectly

BeneHTWG, 2023-09-20:
in #32, the localization is safed after switching to automatic mode and after each pulse interrupt, but somehow only the first storage is not overwritten. The deserialization in the localization init still works properly, so the system can be run in automatic mode immediately, but the last safed current position might be wrong

Closed 2023-09-21.

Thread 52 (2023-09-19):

fix localization routine

derfinke, 2023-09-19:
Localization is currently slightly broken, is_triggered has to be kept at true to properly function

BeneHTWG, 2023-09-20:
localization now works properly after cleanup in #32

Closed 2023-09-20.

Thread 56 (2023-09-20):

fix speed ramp bug

BeneHTWG, 2023-09-20:
currently in few cases, the motor directly runs in full speed and skips the ramp

Closed 2023-09-21.

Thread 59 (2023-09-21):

trigger localization reset when button is still pressed

BeneHTWG, 2023-09-21:
- currently the long press for localization reset is evaluated, after releasing the button
- not so nice, as its not clear, when to release the button

Closed 2023-10-04.

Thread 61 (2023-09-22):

reduce pulse interrupt function

BeneHTWG, 2023-09-22:
possibly too much code in the interrupt disturbes correct position calculation

Closed 2023-09-22.

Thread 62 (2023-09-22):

add linear guide errorhandler

BeneHTWG, 2023-09-22:
- add error ID member to linear guide struct
- add function to linearguide_update, which checks for errors:
  - (0: normal)
  - 1: motor error -> stop motor
  - 2: high current -> stop motor
  - 3: distance fault -> switch to manual mode and repeat localization
  - 4: strong wind (from controllino put request) -> stop motor
  - > turn on error lamp, set error ID in linear guide struct

Closed 2023-09-28.

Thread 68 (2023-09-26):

adjust pulse to distance relation

BeneHTWG, 2023-09-26:
currently an absolute distance of about 2.2 m is measured between the two end positions via the pulse count, which can't be true
-> compare pulse count after driving to end pos with true distance in mm and change respective defines

BeneHTWG, 2023-09-27:
solved in #62

Closed 2023-09-27.

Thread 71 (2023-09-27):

advanced speed ramp

BeneHTWG, 2023-09-27:
- calculate brake path to trigger negative speed ramp respectively the path before reaching the desired position

- if assuming a constant speed is not accurate, the value of the current sensor could be a sensible parameter to increase the precision of the calculated brake path

- alternative: measure the actual speed with the time between two pulses
- when breaking, leave movement state at back/forward until system actually stopped

Closed 2023-10-04.

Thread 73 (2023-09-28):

function to change speed in rpm

BeneHTWG, 2023-09-28:
- [x] remove all functions to convert between mm/s and rpm
- [x] edit change_speed_mms function to change_speed_rpm
- [ ] update or trigger speedramp when motor currently in movement to change speed directly
- [x] fix IO_analog_write to convert the rpm value to dac before wrtiting to hardware

BeneHTWG, 2023-10-04:
rpm value is set without function now

Closed 2023-10-04.

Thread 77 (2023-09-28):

extend error handler

BeneHTWG, 2023-09-28:
- add wind fault to linear guide error handler
- change distance fault handling to just adapting counted distance to measured distance
- when reaching endswitches, reset pulse count
- handle windfault with driving to 100% roll
- handle motor and current fault with stopping the motor

Closed 2023-10-01.

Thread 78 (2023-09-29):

linear guide force move

BeneHTWG, 2023-09-29:
- the movement is now handled with giving a desired pos in mm as soon as the position is known -> being in localization state 3 or higher
- this means, that after this state the manual movement does not work with a single call of Linear_Guide_move().
- instead the desired position must be set before
- this would be the "force move" function which is needed in the cgi handler to move the motor from the website manually
- the functionality is already implemented in the manual control move toggle function

Closed 2023-09-30.

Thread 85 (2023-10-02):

Besprechung 02.10.23

derfinke, 2023-10-02:
1. position trimmen rollen + und -

2. Manuelles fahren position merken und anfahren

3. Motorimpulse als referenz wert des Abstandes

4. Abstandswert wird bei zu großem delta als warnung ausgegeben

5. wechselschalter betrieb für automatik manuell

6. DHCP checkbox

7. IP addresse manuell zurücksetzen

BeneHTWG, 2023-10-04:
- the functions [get / set]_[current / desired]_roll_trim_percentage now [return / pass] the percentage as positive or negative value depending on trim or roll mode (1)
- this is already changed in the REST protocoll and in the webserver / ssi_handler but not tested yet @derfinke
- the features (2)...(5) are implemented and tested
- (6) and (7) are not done yet

BeneHTWG, 2023-10-04:
**additional features**

- localization is now safed to FRAM on each position change -> automatic mode on reboot allways possible
- a direct change between forward and backwards is now avoided by queueing the requests, and finishing the brake phase before
- also a brake phase can now be interrupted directly by an acceleration into the current direction

Closed 2024-02-21.

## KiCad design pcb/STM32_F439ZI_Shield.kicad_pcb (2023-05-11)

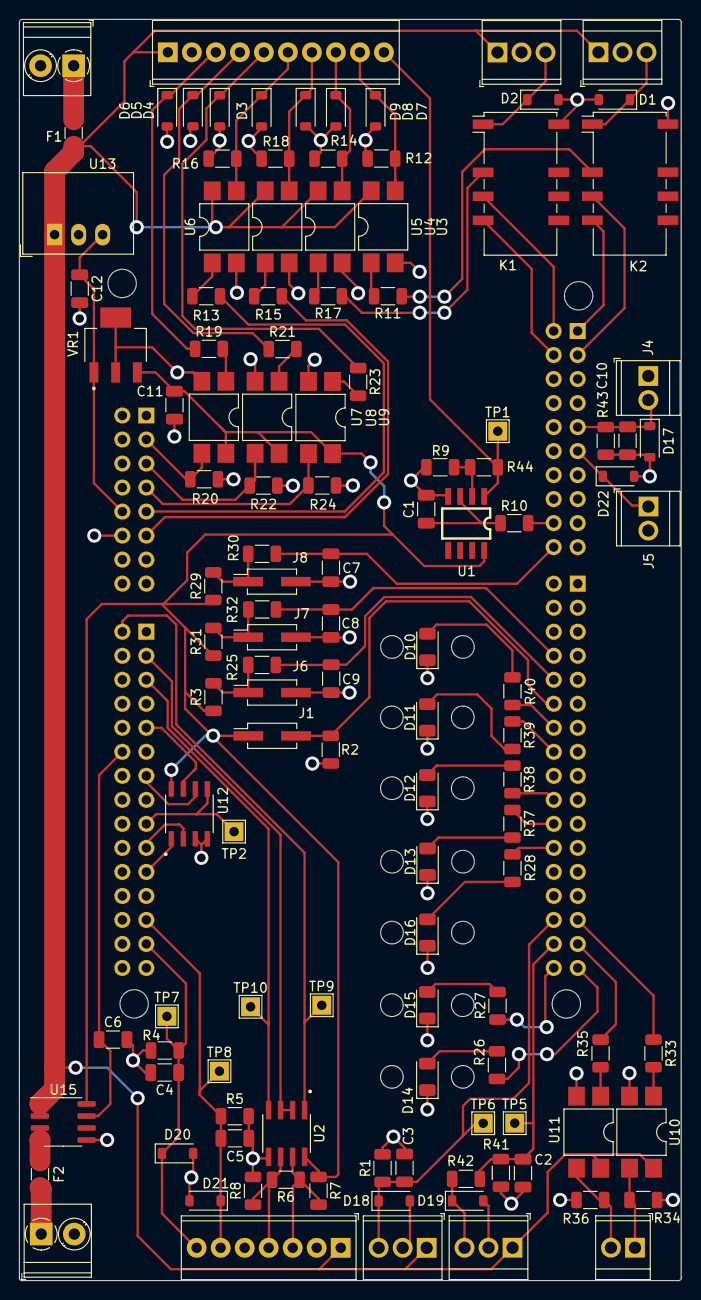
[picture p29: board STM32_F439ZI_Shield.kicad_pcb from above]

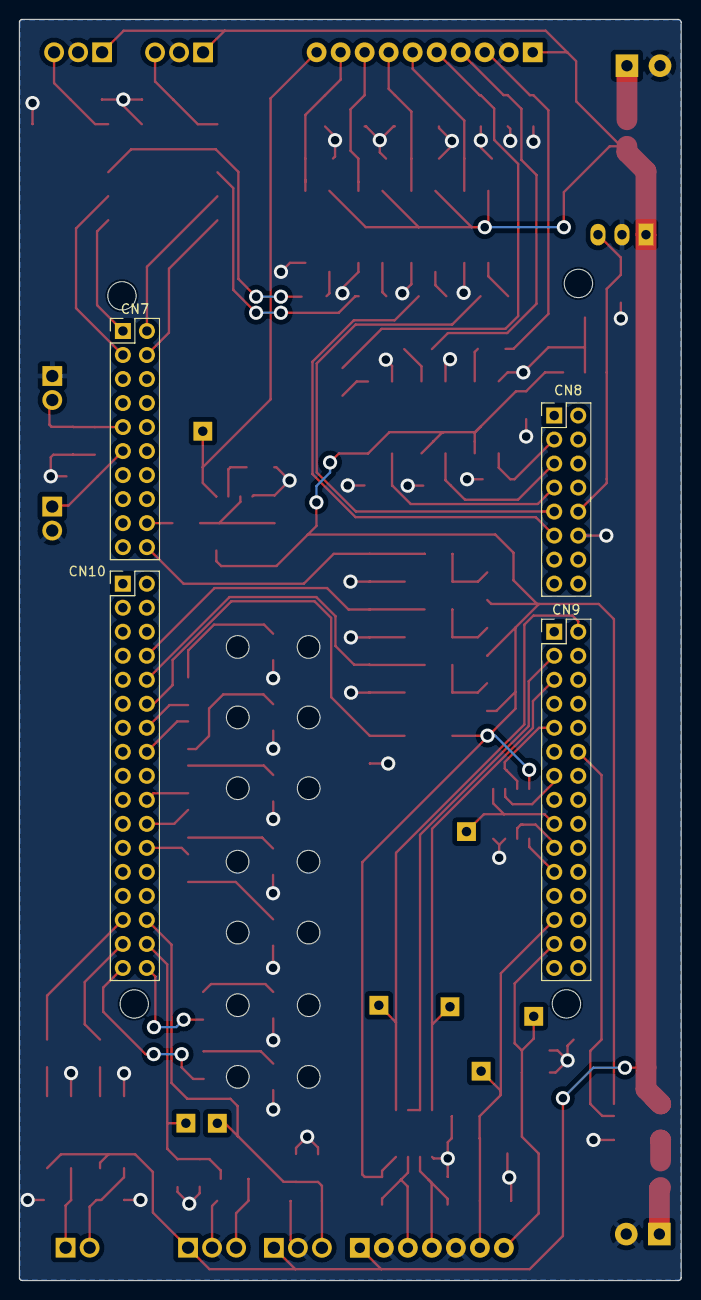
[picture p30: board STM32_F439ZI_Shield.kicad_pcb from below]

Board: 2 copper layers, 70.0 x 133.4 mm, 124 parts (4 on the bottom side), 83 nets.

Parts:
Abstandssensor1: Conn_01x03_Pin; TerminalBlock_TE_282834-3_1x03_P2.54mm_Horizontal
Anenometer1: Conn_01x07_Pin; TerminalBlock_TE_282834-7_1x07_P2.54mm_Horizontal
C1: 22u; C_1206_3216Metric
C2, C3, C4, C5, C6, C10: 22n; C_1206_3216Metric
C7, C8, C9: 220n; C_1206_3216Metric
C11: 33uF; C_1206_3216Metric
C12: 0.47uF; C_1206_3216Metric
CN7: Conn_02x10_Odd_Even; PinHeader_2x10_P2.54mm_Vertical
CN8: Conn_02x08_Odd_Even; PinHeader_2x08_P2.54mm_Vertical
CN9: Conn_02x15_Odd_Even; PinHeader_2x15_P2.54mm_Vertical
CN10: Conn_02x17_Odd_Even; PinHeader_2x17_P2.54mm_Vertical
D1: SMBJ5359B-TP; D_SOD-123
D2, D3, D4, D5, D6, D7, D8, D9: SMPJ5359B-TP; D_SOD-123
D10, D11, D16: LED_Green; LED_1206_3216Metric
D12, D14, D15: LED_Gelb; LED_1206_3216Metric
D13: LED_Red; LED_1206_3216Metric
D17, D18, D19, D20, D21, D22: KDZVTR6.8B; D_SOD-123
Endschalter_Hinten1: Conn_01x03_Pin; TerminalBlock_TE_282834-3_1x03_P2.54mm_Horizontal
Endschalter_Vorne1: Conn_01x03_Pin; TerminalBlock_TE_282834-3_1x03_P2.54mm_Horizontal
F1, F2: Fuse; Fuse_1206_3216Metric
J1, J6, J7, J8: Conn_01x02_Pin; PinHeader_2x01_P2.54mm_Vertical_SMD
J3: Relais_Conn; TerminalBlock_TE_282834-2_1x02_P2.54mm_Horizontal
J4, J5: Conn_01x02_Pin; TerminalBlock_TE_282834-2_1x02_P2.54mm_Horizontal
K1, K2: G6S-2; Relay_DPDT_Omron_G6S-2F
Kraftmessung1: Conn_01x04_Pin; TerminalBlock_TE_282834-3_1x03_P2.54mm_Horizontal
Motor_Logik1: Conn_01x10_Pin; TerminalBlock_TE_1-282834-0_1x10_P2.54mm_Horizontal
Motor_Spannungsversorgung1: Conn_01x02_Pin; TerminalBlock_Phoenix_PT-1,5-2-3.5-H_1x02_P3.50mm_Horizontal
R1, R4, R5, R28, R39, R40, R43: 150; R_1206_3216Metric
R2, R3, R9, R29, R31: 10k; R_1206_3216Metric
R6, R26, R27, R38: 120; R_1206_3216Metric
R7, R8: 750; R_1206_3216Metric
R10: 240; R_1206_3216Metric
R11, R13, R15, R17, R33, R35: 700; R_1206_3216Metric
R12, R14, R16, R18, R34, R36: 11k; R_1206_3216Metric
R19, R21, R23: 2,2k; R_1206_3216Metric
R20, R22, R24: 6,8k; R_1206_3216Metric
R25, R30, R32: 36k; R_1206_3216Metric
R37: 110; R_1206_3216Metric
R41: 2300; R_1206_3216Metric
R42: 1000; R_1206_3216Metric
R44: 0; R_1206_3216Metric
Spannungsversorgung_1: Conn_01x02_Pin; TerminalBlock_Phoenix_PT-1,5-2-3.5-H_1x02_P3.50mm_Horizontal
TP1, TP2, TP5, TP6, TP7, TP8, TP9, TP10: TestPoint; TestPoint_THTPad_2.0x2.0mm_Drill1.0mm
U1: LM2904; SO08
U2: MAX3485; SOIC127P600X175-8N
U3, U4, U5, U6, U7, U8, U9, U10, U11: LTV-817S; SMDIP-4_W7.62mm
U12: FL25L16B; SOIC127P602X172-8N
U13: R-78E-5.0-1.0; Converter_DCDC_RECOM_R-78E-0.5_THT
U15: ACS724xLCTR-05AB; SOIC-8_3.9x4.9mm_P1.27mm
VR1: LM3940IMP-3.3/NOPB; VREG_LM3940IMP-3.3_NOPB

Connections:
+3.3V: C11.1, J1.1, R3.1, R7.1, R29.1, R31.1, U1.8 (V+), U2.8 (VCC), U7.4, U8.4, U9.4, U12.8 (VDD), U15.8 (VCC), VR1.3 (OUT)
+5V: C12.1, CN8.10, U13.3 (OUT), VR1.1 (IN)
+24V: Abstandssensor1.1, Anenometer1.1, Endschalter_Hinten1.1, Endschalter_Vorne1.1, F1.2, Kraftmessung1.1, Motor_Logik1.1, U3.4, U4.4, U5.4, U6.4, U10.4, U11.4, U13.1 (IN), U15.1 (IP+), U15.2 (IP+)
/Buttons_LEDS/MCU_Kalibrierung: C9.1, CN10.10, R25.2
/Buttons_LEDS/MCU_LED_Betrieb: CN10.16, R39.1
/Buttons_LEDS/MCU_LED_Kalibrierung: CN10.24, R28.1
/Buttons_LEDS/MCU_LED_Manuell: CN10.20, R38.1
/Buttons_LEDS/MCU_LED_PWR: CN10.14, R40.1
/Buttons_LEDS/MCU_LED_Rollen: CN10.34, R27.1
/Buttons_LEDS/MCU_LED_Stoerung: CN10.22, R37.1
/Buttons_LEDS/MCU_LED_Trimmen: CN10.33, R26.1
/Buttons_LEDS/MCU_Switch: CN10.12, J1.2, R2.2
/Buttons_LEDS/MCU_Vorfahren: C7.1, CN7.20, R30.2
/Buttons_LEDS/MCU_Zurueckfahren: C8.1, CN10.8, R32.2
/Enable: CN9.3, U2.2 (~RE), U2.3 (DE)
/Endschalter/Endschalter_Hinten: D2.1 (K), Endschalter_Hinten1.3, K1.1
/Endschalter/Endschalter_Vorne: D1.1 (K), Endschalter_Vorne1.3, K2.1
/Motor/Drehzahl_Analog_OUT: Motor_Logik1.10, R44.1, TP1.1, U1.1
/Motor/IN0_OUT: D7.1 (K), Motor_Logik1.9, R12.1, U3.3
/Motor/IN1_OUT: D8.1 (K), Motor_Logik1.8, R14.1, U4.3
/Motor/IN2_OUT: D9.1 (K), Motor_Logik1.7, R18.1, U5.3
/Motor/IN3_OUT: D3.1 (K), Motor_Logik1.6, R16.1, U6.3
/Motor/OUT1_IN: D6.1 (K), Motor_Logik1.3, R19.1
/Motor/OUT2_IN: D5.1 (K), Motor_Logik1.4, R21.1
/Motor/OUT3_IN: D4.1 (K), Motor_Logik1.5, R23.1
/Motor/Stromsensor_MCU: C6.1, CN9.12, U15.7 (VIOUT)
/Optokoppler/Ext_Relais1_MCU: CN10.29, R33.1
/Optokoppler/Ext_Relais1_OUT: J3.1, R34.1, U10.3
/Optokoppler/Ext_Relais2_MCU: CN10.31, R35.1
/Optokoppler/Ext_Relais2_OUT: J3.2, R36.1, U11.3
/Optokoppler/IN0_MCU_IN: K2.3, R11.1
/Optokoppler/IN1_MCU_IN: K1.3, R17.1
/Optokoppler/IN2_MCU_IN: CN8.11, R15.1
/Optokoppler/IN3_MCU_IN: CN8.9, R13.1
/Optokoppler/OUT1_MCU: CN8.3, R20.1, U7.3
/Optokoppler/OUT2_MCU: CN8.5, R22.1, U8.3
/Optokoppler/OUT3_MCU: CN8.7, R24.1, U9.3
/Rx: CN9.2, TP9.1, U2.1 (RO)
/STM32F439ZI/Abstandsmessung_MCU: Abstandssensor1.3, C3.1, CN10.30, D18.1 (K), R1.1, TP6.1
/STM32F439ZI/CS: CN9.21, U12.1 (~CS)
/STM32F439ZI/Drehzahl_Analog_OUT: CN7.18, R10.2
/STM32F439ZI/Endschalter_Hinten_MCU: CN7.4, K1.5
/STM32F439ZI/Endschalter_Vorne_MCU: CN7.1, K2.5
/STM32F439ZI/HOLD: CN9.9, U12.7 (~HOLD)
/STM32F439ZI/IN0_MCU: CN7.3, K2.4
/STM32F439ZI/IN1_MCU: CN7.2, K1.4
/STM32F439ZI/Kraftmessung_MCU: C2.1, CN10.32, R41.1, R42.1, TP5.1
/STM32F439ZI/MISO: CN9.17, TP2.1, U12.5 (SI)
/STM32F439ZI/MOSI: CN9.19, U12.2 (SO)
/STM32F439ZI/Opt_Analog_IN: CN7.11, D22.1 (K), J5.1
/STM32F439ZI/Opt_Temperaturmessung: C10.1, CN7.9, D17.1 (K), J4.2, R43.1
/STM32F439ZI/SCK: CN9.13, U12.6 (SCK)
/STM32F439ZI/Windgeschwindigkeit_MCU: Anenometer1.7, C4.1, CN9.27, D20.1 (K), R4.1, TP7.1
/STM32F439ZI/Windrichtung_MCU: Anenometer1.6, C5.1, CN9.25, D21.1 (K), R5.1, TP8.1
/Sensoren_Eingänge/RS485_RX_TX_NEG_1: Anenometer1.3, R6.1, R7.2, U2.7 (B)
/Sensoren_Eingänge/RS485_RX_TX_POS_1: Anenometer1.4, R6.2, R8.1, U2.6 (A)
/Tx: CN9.5, TP10.1, U2.4 (DI)
GND: Abstandssensor1.2, Anenometer1.2, Anenometer1.5, C1.2, C2.2, C3.2, C4.2, C5.2, C6.2, C7.2, C8.2, C9.2, C10.2, C11.2, C12.2, CN8.12, D1.2 (A), D2.2 (A), D3.2 (A), D4.2 (A), D5.2 (A), D6.2 (A), D7.2 (A), D8.2 (A), D9.2 (A), D10.1 (K), D11.1 (K), D12.1 (K), D13.1 (K), D14.1 (K), D15.1 (K), D16.1 (K), D17.2 (A), D18.2 (A), D19.2 (A), D20.2 (A), D21.2 (A), D22.2 (A), Endschalter_Hinten1.2, Endschalter_Vorne1.2, J4.1, J5.2, J6.2, J7.2, J8.2, K1.12, K2.12, Kraftmessung1.2, Motor_Logik1.2, Motor_Spannungsversorgung1.2, R1.2, R2.1, R4.2, R5.2, R8.2, R9.2, R12.2, R14.2, R16.2, R18.2, R20.2, R22.2, R24.2, R34.2, R36.2, R42.2, R43.2, Spannungsversorgung_1.2, U1.4 (V-), U2.5 (GND), U3.2, U4.2, U5.2, U6.2, U7.2, U8.2, U9.2, U10.2, U11.2, U12.3 (~WP), U12.4 (GND), U13.2 (GND), U15.5 (GND), VR1.2 (GND_2), VR1.4 (GND_4)
unnamed: D10.2 (A), R40.2
unnamed: D11.2 (A), R39.2
unnamed: D12.2 (A), R38.2
unnamed: D13.2 (A), R37.2
unnamed: D14.2 (A), R26.2
unnamed: D15.2 (A), R27.2
unnamed: D16.2 (A), R28.2
unnamed: D19.1 (K), Kraftmessung1.3, R41.2
unnamed: F2.2, U15.3 (IP-), U15.4 (IP-)
unnamed: J6.1, R3.2, R25.1
unnamed: J7.1, R31.2, R32.1
unnamed: J8.1, R29.2, R30.1
unnamed: F2.1, Motor_Spannungsversorgung1.1
unnamed: R11.2, U3.1
unnamed: R13.2, U6.1
unnamed: R15.2, U5.1
unnamed: R17.2, U4.1
unnamed: R19.2, U7.1
unnamed: R21.2, U8.1
unnamed: R23.2, U9.1
unnamed: R33.2, U10.1
unnamed: R35.2, U11.1
unnamed: F1.1, Spannungsversorgung_1.1
unnamed: C1.1, R10.1, U1.3 (+)
unnamed: R9.1, R44.2, U1.2 (-)

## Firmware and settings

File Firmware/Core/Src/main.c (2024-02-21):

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
/* Includes ------------------------------------------------------------------*/
#include "main.h"
#include "lwip.h"

/* USER CODE BEGIN Includes */
#include "FRAM.h"
#include "WSWD.h"
#include "Manual_Control.h"
#include "Test.h"
#include "httpd.h"
#include "tcp_server.h"
#include "http_ssi_cgi.h"

/* USER CODE END Includes */

/* USER CODE BEGIN PD */
#define ABSTAND_TEST 0
#define STROM_TEST 0
#define WIND_TEST 0
/* USER CODE END PD */

ADC_HandleTypeDef hadc1;
ADC_HandleTypeDef hadc2;
ADC_HandleTypeDef hadc3;

DAC_HandleTypeDef hdac;

SPI_HandleTypeDef hspi4;

TIM_HandleTypeDef htim2;
TIM_HandleTypeDef htim10;
TIM_HandleTypeDef htim11;

UART_HandleTypeDef huart1;
UART_HandleTypeDef huart2;
UART_HandleTypeDef huart3;

/* USER CODE BEGIN PV */

static Linear_Guide_t *linear_guide = {0};
static Manual_Control_t manual_control;

char Rx_buffer[20];

/* USER CODE END PV */

void SystemClock_Config(void);
static void MX_GPIO_Init(void);
static void MX_USART3_UART_Init(void);
static void MX_ADC1_Init(void);
static void MX_ADC2_Init(void);
static void MX_ADC3_Init(void);
static void MX_DAC_Init(void);
static void MX_USART2_UART_Init(void);
static void MX_SPI4_Init(void);
static void MX_USART1_UART_Init(void);
static void MX_TIM2_Init(void);
static void MX_TIM10_Init(void);
static void MX_TIM11_Init(void);
/* USER CODE BEGIN 0 */
PUTCHAR_PROTOTYPE
{
  /* Place your implementation of fputc here */
  /* e.g. write a character to the USART1 and Loop until the end of transmission */
  HAL_UART_Transmit(&huart3, (uint8_t *)&ch, 1, 0xFFFF);

  return ch;
}
/* USER CODE END 0 */

/**
  * @brief  The application entry point.
  * @retval int
  */
int main(void)
{
  /* USER CODE BEGIN 1 */
	hdac.State = HAL_DAC_STATE_RESET;
  /* USER CODE END 1 */

  /* MCU Configuration--------------------------------------------------------*/

  /* Reset of all peripherals, Initializes the Flash interface and the Systick. */
  HAL_Init();

  /* Configure the system clock */
  SystemClock_Config();

  /* Initialize all configured peripherals */
  MX_GPIO_Init();
  MX_USART3_UART_Init();
  MX_ADC1_Init();
  MX_ADC2_Init();
  MX_ADC3_Init();
  MX_DAC_Init();
  MX_USART2_UART_Init();
  MX_SPI4_Init();
  MX_USART1_UART_Init();
  MX_LWIP_Init();
  MX_TIM2_Init();
  MX_TIM10_Init();
  MX_TIM11_Init();
  /* USER CODE BEGIN 2 */
  IO_init_distance_sensor(&hadc1);
  IO_init_current_sensor(&hadc3);
  Linear_Guide_init(&hdac, &htim11);
  linear_guide = LG_get_Linear_Guide();
  manual_control = Manual_Control_init(linear_guide, &htim10);

  printf("Sailwind Firmware Ver. 1.0\r\n");

#if LED_TEST
  LED_toggle(&linear_guide.leds.center_pos_set);
  LED_toggle(&linear_guide.leds.error);
  LED_toggle(&linear_guide.leds.manual);
  LED_toggle(&linear_guide.leds.automatic);
  LED_toggle(&linear_guide.leds.rollung);
  LED_toggle(&linear_guide.leds.trimmung);
#endif
#if MOTOR_TEST
  motor_start_moving(&linear_guide.motor, motor_moving_state_rechtslauf);
#endif

#if FRAM_TEST
  uint8_t test[4];
  memset(test, 0, sizeof(test));
  FRAM_init();
  FRAM_write((uint8_t*)"Test", 0x0000, 4);
  HAL_Delay(5);
  FRAM_read(0x0000, test, sizeof(test));
  printf("read from FRAM: %u\r\n", test);
#endif

#if WIND_TEST
  char NMEA[31];
  float speed = 0.0;
  float dir = 0.0;
  WSWD_receive_NMEA(NMEA);
  printf("%s",NMEA);
  WSWD_get_wind_infos(NMEA, &speed, &dir);
  printf("speed:%f, dir:%f\r\n", speed, dir);
#endif

  tcp_server_init();
  http_server_init();

  /* USER CODE END 2 */

  /* Infinite loop */
  /* USER CODE BEGIN WHILE */
  while (1)
  {
      MX_LWIP_Process();
      if (Linear_Guide_update(linear_guide) == LG_UPDATE_NORMAL)
      {
    	  //Test_uart_poll(&huart3, Rx_buffer, &manual_control);
    	  Manual_Control_poll(&manual_control);
    	  Manual_Control_Localization(&manual_control);
      }
      /*
       * add tcp handling
       */
    /* USER CODE END WHILE */

    /* USER CODE BEGIN 3 */

  }
  /* USER CODE END 3 */
}

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
/* USER CODE BEGIN 4 */
void HAL_GPIO_EXTI_Callback(uint16_t GPIO_Pin) {
  Linear_Guide_callback_motor_pulse_capture(linear_guide);
}

void HAL_TIM_PeriodElapsedCallback(TIM_HandleTypeDef *htim)
{
  // Check which version of the timer triggered this callback and toggle LED
  if (htim == &htim2 )
  {
    printf("executing reset\r\n");
    HAL_TIM_Base_Stop(&htim2);
    HAL_TIM_Base_Stop_IT(&htim2);
    HAL_NVIC_SystemReset();
  }
  else if (htim == manual_control.htim_reset_ptr)
  {
	  Manual_Control_long_press_callback(&manual_control);
  }
  else if (htim == linear_guide->leds.htim_blink_ptr)
  {
	  LED_blink_callback(htim);
  }
}
/* USER CODE END 4 */
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


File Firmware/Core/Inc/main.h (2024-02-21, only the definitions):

#define PUTCHAR_PROTOTYPE int __io_putchar(int ch)
#define SPI4_CS_Pin GPIO_PIN_3
#define SPI4_CS_GPIO_Port GPIOE
#define Switch_Betriebsmodus_Pin GPIO_PIN_4
#define Switch_Betriebsmodus_GPIO_Port GPIOF
#define Windrichtungmessung_Pin GPIO_PIN_7
#define Windrichtungmessung_GPIO_Port GPIOF
#define Windgeschwindigkeitmessung_Pin GPIO_PIN_9
#define Windgeschwindigkeitmessung_GPIO_Port GPIOF
#define Strommessung_Pin GPIO_PIN_10
#define Strommessung_GPIO_Port GPIOF
#define MCO_Pin GPIO_PIN_0
#define MCO_GPIO_Port GPIOH
#define RMII_MDC_Pin GPIO_PIN_1
#define RMII_MDC_GPIO_Port GPIOC
#define Kalibrierung_Pin GPIO_PIN_2
#define Kalibrierung_GPIO_Port GPIOC
#define Abstandsmessung_Pin GPIO_PIN_0
#define Abstandsmessung_GPIO_Port GPIOA
#define RMII_REF_CLK_Pin GPIO_PIN_1
#define RMII_REF_CLK_GPIO_Port GPIOA
#define RMII_MDIO_Pin GPIO_PIN_2
#define RMII_MDIO_GPIO_Port GPIOA
#define Windsensor_Rx_Pin GPIO_PIN_3
#define Windsensor_Rx_GPIO_Port GPIOA
#define Drehzahl_DAC_OUT_Pin GPIO_PIN_4
#define Drehzahl_DAC_OUT_GPIO_Port GPIOA
#define Analog_IN_Optional_Pin GPIO_PIN_6
#define Analog_IN_Optional_GPIO_Port GPIOA
#define RMII_CRS_DV_Pin GPIO_PIN_7
#define RMII_CRS_DV_GPIO_Port GPIOA
#define RMII_RXD0_Pin GPIO_PIN_4
#define RMII_RXD0_GPIO_Port GPIOC
#define RMII_RXD1_Pin GPIO_PIN_5
#define RMII_RXD1_GPIO_Port GPIOC
#define Kraftmessung_Pin GPIO_PIN_0
#define Kraftmessung_GPIO_Port GPIOB
#define Button_Forward_Pin GPIO_PIN_1
#define Button_Forward_GPIO_Port GPIOB
#define LED_Automatik_Pin GPIO_PIN_2
#define LED_Automatik_GPIO_Port GPIOB
#define Betriebsmodus_2_Nur_Prototyp_Pin GPIO_PIN_12
#define Betriebsmodus_2_Nur_Prototyp_GPIO_Port GPIOF
#define Betriebsmodus_Prototyp_Pin GPIO_PIN_15
#define Betriebsmodus_Prototyp_GPIO_Port GPIOF
#define Ext_Relais_1_Pin GPIO_PIN_15
#define Ext_Relais_1_GPIO_Port GPIOE
#define Ext_Relais_2_Pin GPIO_PIN_10
#define Ext_Relais_2_GPIO_Port GPIOB
#define LED_set_center_Pin GPIO_PIN_11
#define LED_set_center_GPIO_Port GPIOB
#define RMII_TXD1_Pin GPIO_PIN_13
#define RMII_TXD1_GPIO_Port GPIOB
#define Endschalter_Hinten_Pin GPIO_PIN_15
#define Endschalter_Hinten_GPIO_Port GPIOB
#define STLK_RX_Pin GPIO_PIN_8
#define STLK_RX_GPIO_Port GPIOD
#define STLK_TX_Pin GPIO_PIN_9
#define STLK_TX_GPIO_Port GPIOD
#define LED_Pitch_Pin GPIO_PIN_11
#define LED_Pitch_GPIO_Port GPIOD
#define LED_Stoerung_Pin GPIO_PIN_12
#define LED_Stoerung_GPIO_Port GPIOD
#define LED_Manuell_Pin GPIO_PIN_13
#define LED_Manuell_GPIO_Port GPIOD
#define IN_1_Pin GPIO_PIN_6
#define IN_1_GPIO_Port GPIOC
#define OUT_1_Pin GPIO_PIN_9
#define OUT_1_GPIO_Port GPIOC
#define OUT_1_EXTI_IRQn EXTI9_5_IRQn
#define OUT_2_Pin GPIO_PIN_10
#define OUT_2_GPIO_Port GPIOC
#define OUT_3_Pin GPIO_PIN_11
#define OUT_3_GPIO_Port GPIOC
#define IN_3_Pin GPIO_PIN_12
#define IN_3_GPIO_Port GPIOC
#define IN_2_Pin GPIO_PIN_2
#define IN_2_GPIO_Port GPIOD
#define HOLD_Pin GPIO_PIN_3
#define HOLD_GPIO_Port GPIOD
#define Windsensor_Tx_Pin GPIO_PIN_5
#define Windsensor_Tx_GPIO_Port GPIOD
#define Windsensor_EN_Pin GPIO_PIN_6
#define Windsensor_EN_GPIO_Port GPIOD
#define RMII_TX_EN_Pin GPIO_PIN_11
#define RMII_TX_EN_GPIO_Port GPIOG
#define RMII_TXD0_Pin GPIO_PIN_13
#define RMII_TXD0_GPIO_Port GPIOG
#define Button_Backwards_Pin GPIO_PIN_4
#define Button_Backwards_GPIO_Port GPIOB
#define LED_PWR_Pin GPIO_PIN_6
#define LED_PWR_GPIO_Port GPIOB
#define Endschalter_Vorne_Pin GPIO_PIN_8
#define Endschalter_Vorne_GPIO_Port GPIOB
#define IN_0_Pin GPIO_PIN_9
#define IN_0_GPIO_Port GPIOB
#define LED_Roll_Pin GPIO_PIN_0
#define LED_Roll_GPIO_Port GPIOE

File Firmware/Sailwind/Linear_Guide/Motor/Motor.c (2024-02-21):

/*
 * Motor.c
 *
 *  Created on: 20.04.2023
 *      Author: Bene
 */

#include "Motor.h"
#include <stdlib.h>
#include "FRAM.h"
#include "FRAM_memory_mapping.h"

/* defines ------------------------------------------------------------*/
#define MOTOR_RPM_MAX 4378.44F // corresponds to ANALOG_MAX (4096) and max output voltage of 10.7 V -> 4092 rpm corresponds to 10 V (BG 45 SI manual)
#define MOTOR_RPM_NOMINAL 3000.0F// nominal speed
#define MOTOR_NORMAL_SPEED 1600

/* private function prototypes -----------------------------------------------*/
static uint16_t Motor_read_max_speed(void);
static IO_analogActuator_t Motor_AIN_init(DAC_HandleTypeDef *hdac_ptr);
static void Motor_press_enter_to_continue();


/* API function definitions -----------------------------------------------*/
Motor_t Motor_init(DAC_HandleTypeDef *hdac_ptr) {
	Motor_t motor = {
			.current_function = Motor_function_stop,
			.INs = {
					IO_digital_Out_Pin_init(IN_0_GPIO_Port, IN_0_Pin, GPIO_PIN_RESET),
					IO_digital_Out_Pin_init(IN_1_GPIO_Port, IN_1_Pin, GPIO_PIN_RESET),
					IO_digital_Out_Pin_init(IN_2_GPIO_Port, IN_2_Pin, GPIO_PIN_RESET),
					IO_digital_Out_Pin_init(IN_3_GPIO_Port, IN_3_Pin, GPIO_PIN_RESET),
			},
			.AIN_set_rpm = Motor_AIN_init(hdac_ptr),
			.OUT2_error = IO_digital_Pin_init(OUT_2_GPIO_Port, OUT_2_Pin),
			.OUT3_rot_dir = IO_digital_Pin_init(OUT_3_GPIO_Port, OUT_3_Pin),
			.rpm_set_point = 0,
			.normal_rpm = Motor_read_max_speed(),
			.ramp_final_rpm = 0,
			.ramp_activated = False
	};
	return motor;
}
/* void motor_start_moving(Motor_t *motor_ptr, motor_moving_state_t direction)
 *  Description:
 *   - write digital motor Inputs to start motor movement in desired direction (motor_moving_state_rechtslauf / ...linkslauf)
 */
void Motor_start_moving(Motor_t *motor_ptr, Motor_function_t direction) {
	printf("motor start moving\r\n");
	Motor_set_function(motor_ptr, direction);
	motor_ptr->ramp_final_rpm = motor_ptr->normal_rpm;
	motor_ptr->ramp_activated = True;
}
/* void motor_stop_moving(Motor_t *motor_ptr)
 *  Description:
 *   - write digital motor Inputs to stop the motor
 *   - save the new moving state to the motor reference
 */
void Motor_stop_moving(Motor_t *motor_ptr, boolean_t immediate) {
	printf("motor stop moving\r\n");
	if (immediate)
	{
		Motor_set_rpm(motor_ptr, 0);
	}
	else
	{
		motor_ptr->ramp_final_rpm = 0;
		motor_ptr->ramp_activated = True;
	}
}

int8_t Motor_speed_ramp(Motor_t *motor_ptr)
{
	if (!motor_ptr->ramp_activated)
	{
		return MOTOR_RAMP_INACTIVE;
	}
	if (abs(motor_ptr->rpm_set_point - motor_ptr->ramp_final_rpm) < MOTOR_RAMP_STEP_RPM)
	{
		Motor_set_rpm(motor_ptr, motor_ptr->ramp_final_rpm);
		motor_ptr->ramp_activated = False;
		if (motor_ptr->rpm_set_point == 0)
		{
			return MOTOR_RAMP_STOPPED;
		}
		return MOTOR_RAMP_NORMAL_SPEED;
	}
	if ((HAL_GetTick()-motor_ptr->ramp_last_step_ms) < MOTOR_RAMP_STEP_MS)
	{
		return MOTOR_RAMP_WAIT;
	}
	int8_t sign = motor_ptr->ramp_final_rpm == 0 ? -1 : 1;
	Motor_set_rpm(motor_ptr, motor_ptr->rpm_set_point + sign * MOTOR_RAMP_STEP_RPM);
	motor_ptr->ramp_last_step_ms = HAL_GetTick();
	return MOTOR_RAMP_NEXT_STEP;
}

boolean_t Motor_is_currently_braking(Motor_t motor)
{
	return motor.ramp_activated && motor.ramp_final_rpm == 0;
}

/* void motor_set_function(Motor_t *motor_ptr, motor_function_t function)
 *  Description:
 *   - convert the "function" enum (0..7) to a binary number between 00 and 11 to set the digital motor Inputs as following:
 *   - function |IN0 	IN1 |IN2	IN3	|meaning
 *     ---------------------------------------------------------
 *   		0	|0		0	|-		-	|aus
 *   		1	|1		0	|-		-	|rechtslauf
 *   		2	|0		1	|-		-	|linkslauf
 *   		3	|1		1	|-		-	|stopp mit haltemoment
 *   		4	|-		-	|0		0	|drehzahlvorgabe
 *   		5	|-		-	|1		0	|stromvorgabe
 *   		6	|-		-	|0		1	|speed1
 *   		7	|-		-	|1		1	|speed2
 *   - the digits are calculated separately in a for loop that does a bitwise "and" operation with the value 2 and the function value and checks, if the result is != 0
 *   - afterwards the function value is left shifted and the process is repeated for the second digit
 */
void Motor_set_function(Motor_t *motor_ptr, Motor_function_t function) {
	motor_ptr->current_function = function;
	uint8_t pin_offset = (function >= 4) * 2;  // 0 or 2 -> write IN0+0, IN1+0 or IN0+2, IN1+2
	int8_t function_bits = function - pin_offset * 2;  //subtract 4 to function id if its >= 4 -> convert number {0..3} to binary in following for loop
	for (int i = 0; i < 2; i++) {  // write IN0 and IN1 (function in {0..3}) or IN2 and IN3 (function in {4..7}
		GPIO_PinState state = function_bits & 2 ? GPIO_PIN_SET : GPIO_PIN_RESET;  // example: function = 3_d = 11_b, 2_d == 10_b -> 11 & 10 = 10  -> 10 != 0 -> 1
		uint8_t IN_idx = i + pin_offset;  //       function << 1 -> 110_b             -> 110 & 10 = 10 -> 10 != 0 -> 1
		IO_digitalWrite(&motor_ptr->INs[IN_idx], state);
		function_bits <<= 1;
	}
}

/* void Motor_set_rpm(Motor_t *motor_ptr, uint16_t rpm_value)
 *  Description:
 *   - set digital INs of the motor to configure its engine speed
 *   - send an analog value (converted from rpm - valaue) to the analog Input of the motor
 *   - or set default speeds
 */
void Motor_set_rpm(Motor_t *motor_ptr, uint16_t rpm_value)
{
    motor_ptr->rpm_set_point = rpm_value;
    IO_analogWrite(&motor_ptr->AIN_set_rpm, (float) motor_ptr->rpm_set_point);
    Motor_function_t motor_function = Motor_function_velocity_setting;
    if (rpm_value == 0)
    {
    	motor_function = Motor_function_stop;
    }
    Motor_set_function(motor_ptr, motor_function);
}

boolean_t Motor_error(Motor_t *motor_ptr) {
	if (IO_digitalRead(&motor_ptr->OUT2_error) == GPIO_PIN_RESET) {
		return True;
	}
	return False;
}
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

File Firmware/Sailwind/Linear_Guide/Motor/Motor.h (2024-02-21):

/*
 * motor_API.h
 *
 *  Created on: 20.04.2023
 *      Author: Bene
 */

#ifndef MOTOR_MOTOR_H_
#define MOTOR_MOTOR_H_

#include "IO.h"

/* defines ------------------------------------------------------------*/
#define MOTOR_PULSE_PER_ROTATION 12 //public
#define MOTOR_RPM_SPEED_1 75
#define MOTOR_RPM_SPEED_2 150
#define MOTOR_DIRECTION_CCW GPIO_PIN_SET
#define MOTOR_DIRECTION_CW GPIO_PIN_RESET
#define MOTOR_IN_COUNT 4
#define MOTOR_RAMP_STEP_MS 13
#define MOTOR_RAMP_STEP_RPM 10
#define MOTOR_RAMP_INACTIVE 1
#define MOTOR_RAMP_WAIT 2
#define MOTOR_RAMP_NEXT_STEP 3
#define MOTOR_RAMP_NORMAL_SPEED 4
#define MOTOR_RAMP_STOPPED 5


/* typedefs -----------------------------------------------------------*/
typedef enum {
	Motor_function_stop,
	Motor_function_cw_rotation,
	Motor_function_ccw_rotation,
	Motor_function_stop_holding_torque,
	Motor_function_velocity_setting,
	Motor_function_current_setting,
	Motor_function_speed1,
	Motor_function_speed2
} Motor_function_t;

typedef IO_digitalPin_t Motor_INs_t[MOTOR_IN_COUNT];


typedef struct {
	Motor_function_t current_function;
	Motor_INs_t INs;
	IO_analogActuator_t AIN_set_rpm;
	IO_digitalPin_t OUT2_error;
	IO_digitalPin_t OUT3_rot_dir;
	uint16_t normal_rpm;
	uint16_t rpm_set_point;
	uint16_t ramp_final_rpm;
	uint32_t ramp_last_step_ms;
	boolean_t ramp_activated;
} Motor_t;


/* API function prototypes -----------------------------------------------*/
Motor_t Motor_init(DAC_HandleTypeDef *hdac_ptr);
void Motor_start_moving(Motor_t *motor_ptr, Motor_function_t function);
void Motor_stop_moving(Motor_t *motor_ptr, boolean_t immediate);
int8_t Motor_speed_ramp(Motor_t *motor_ptr);
void Motor_set_function(Motor_t *motor_ptr, Motor_function_t function);
void Motor_set_rpm(Motor_t *motor_ptr, uint16_t rpm_value);
boolean_t Motor_error(Motor_t *motor_ptr);
void Motor_teach_speed(Motor_t *motor_ptr, Motor_function_t speed, uint16_t rpm_value, uint32_t tolerance);
boolean_t Motor_is_currently_braking(Motor_t motor);


#endif /* MOTOR_MOTOR_H_ */

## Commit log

2023-03-23 Update README.md
    drive ordner mit stückliste und komponentendoc verlinkt
2023-03-27 added pcb design for STM32Shield
    [STM32.kicad_sch, STM32_F439ZI_Shield.kicad_pcb, STM32_F439ZI_Shield.kicad_sch]
2023-03-27 added Subsheets vor different component types
    [Endschalter.kicad_sch, STM32_F439ZI_Shield.kicad_sch, analog_in.kicad_sch]
2023-03-28 added new sheet and added sensors
    [Motor.kicad_sch, STM32_F439ZI_Shield.kicad_sch, analog_in.kicad_sch]
2023-03-30 Updated PCB
    [Motor.kicad_sch, STM32.kicad_sch, STM32_F439ZI_Shield.kicad_sch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]
2023-03-30 add dc/dc converter
    [STM32_F439ZI_Shield.kicad_sch]
2023-04-03 added buttons & LEDs
    [Buttons.kicad_sch, STM32.kicad_sch, STM32_F439ZI_Shield.kicad_sch]
2023-04-06 Updated footprints
    [Buttons.kicad_sch, Endschalter.kicad_sch, Motor.kicad_sch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]
2023-04-09 Save pcb cut out
    [STM32.kicad_sch, STM32_F439ZI_Shield.kicad_pcb, STM32_F439ZI_Shield.kicad_sch]
2023-04-13 added struct for analog sensors and function to read adc signal at respective channels
2023-04-17 added methods to control dac and structs for the motor unit
2023-04-20 added motor_API and function to set motor INs by specific function
2023-04-24 added function to measure motor rpm
2023-04-25 finished PCB Design V1.0
    [STM32.kicad_sch, STM32_F439ZI_Shield.kicad_pcb]
2023-04-28 added function to teach motor speed
2023-05-03 added button_API with eventHandler and made private functions static
2023-05-03 added LED_API and renamed pointer with "ptr" ending
2023-05-03 added voltage regulator updated pinout
    [STM32.kicad_sch, STM32_F439ZI_Shield.kicad_pcb, STM32_F439ZI_Shield.kicad_sch]
2023-05-03 adjusted capacitor position
    [STM32_F439ZI_Shield.kicad_pcb]
2023-05-05 added calibration functionality and readme.txt for first test
2023-05-06 updated pcb and assigned correct pins
    [STM32.kicad_sch, STM32_F439ZI_Shield.kicad_pcb, STM32_F439ZI_Shield.kicad_sch]
2023-05-06 Revert "added some new pins"
    This reverts commit 4980527cb6c4fccf87e8775d8e5e0138ca49edcc.
    [Sailwind_Firmware.ioc, main.c, main.h]
2023-05-06 adjusted previous Code to new Pin Layout
2023-05-11 finished assigning pins and creating pcb
    [Motor.kicad_sch, Optokoppler.kicad_sch, STM32.kicad_sch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]
2023-05-25 updated and verified motor_set_function() -> swapped motor_function_links/-rechtslauf
2023-05-25 changed type of analog sensor / actuator value to float
2023-05-26 updated and verified button_eventhandler() renamed IO functions and added digital state_change functions
2023-06-02 renamed private functions, reduced motor.calibration members, converted all division operands to float to increase precision and implemented calibrate_set_center function
2023-06-04 improved setting of operating mode, block manual moving while calibration process and implemented switching LEDs for center_pos and operating mode
2023-06-04 completed LED bar init function
2023-06-06 use motor_moving_state to control manual motor moving
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2023-06-18 added linear_guide_api and out-sourced calibration & endschalter functions from motor_API
2023-06-18 added new modules and activated SPI
2023-06-20 improved calibration process and reduced level of nesting in some functions
2023-06-22 bug fix & pass button state instead of whole button to button event handler
2023-06-22 simplified calibration state machine
2023-06-23 added state diagram for calibration process
2023-07-13 added limitation to analog actuator object
2023-07-25 added test_api for test protocol and prints for testing calibration process
2023-07-25 fixed Uart receive
2023-07-30 enabled tim3 global interrupt
2023-07-31 renamed functions, updated Localization state machine, changed motor Ins design
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2023-08-01 changed functionality of motor rpm setting
2023-08-01 added LED test function
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2023-08-02 added functions for Localization struct (de-)serialization
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2023-08-08 added cppcheck config and added cppcheck stage to Jenkinsfile
2023-08-08 fixed syntax and included Sailwind correctly
    [FRAM.c, main.c]
2023-08-09 tried to fix doxygen input
    [FRAM.c]
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2023-08-14 set pins to correct level reduced clock speed
    [Sailwind_Firmware.ioc]
2023-08-15 added Distance Sensor module and added code formatting file
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2023-08-17 fixed FRAM intzerfacing formatted code
    [FRAM.c]
2023-08-22 added better adc avg
2023-08-26 added adc conversion for current sensor
2023-08-26 removed part of adc initialization
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2023-08-27 corrected procedure for getting current sensor values
    [IO.c]
2023-08-27 added wind direction sensor
2023-09-05 fixed current sensor accuracy
    [IO.c, main.c]
2023-09-16 Revert "added all changes"
    This reverts commit a685cddab527f00897814352e5ad26365b7d36b1.
    [Linear_Guide.c, Manual_Control.c, Motor.c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]
2023-09-17 moved Analog sensor inits to seperate functions
2023-09-17 added reading of current state to linear_guide_init
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2023-09-19 added localization reset feature
    [Manual_Control.c]
2023-09-20 fixed localization and speed ramp
    [IO.c, Linear_Guide.c, Manual_Control.c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]
2023-09-21 reset rpm_setpoint to 0 before activating speed ramp
    [Manual_Control.c, Motor.c]
2023-09-21 accelerated speed ramp and fixed final speed limitation
    [Motor.c]
2023-09-21 for testing, safe localization only when localized and when switching to automatic
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2023-09-23 added ssi tags renamed sensor values to status
2023-09-23 added error handling while saving position
    [Linear_Guide.c]
2023-09-25 added error_codes to all returning functions
    [Linear_Guide.c, Manual_Control.c, Motor.c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]
2023-09-25 tested and fixed current changes
    [Linear_Guide.c, Manual_Control.c, main.c]
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2023-09-25 added correct actions for cgi
    [http_ssi_cgi.c]
2023-09-26 removed sconfig settings of adc / dac channels
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2023-09-26 fixed instance IO_analog_Sensor, Linear_Guide_t passing
    [IO.c, Linear_Guide.c, Motor.c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]
2023-09-26 set correct error flag. motor now stops if different direction is chosen. sail pos is now displayed
    [http_ssi_cgi.c]
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2023-09-27 update inits of linear_guide and added distance sensor member
2023-09-27 add error handler and motor fault check
    [Linear_Guide.c, Manual_Control.c, main.c]
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2023-09-27 restored sconfig in dac init and removed sconfig declarations in adc inits
2023-09-27 bug fix and added absolute start position from distance sensor to fram storage
    [Linear_Guide.c, Manual_Control.c, Motor.c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]
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2023-09-28 added Memory mapping.h and replaced all normal FRAM addresses
    [Linear_Guide.c]
2023-09-28 fixed compile errors from merge
    [Linear_Guide.c, main.c]
2023-09-28 changed error handling and added Endswitch handling in automatic mode
    [Linear_Guide.c, Manual_Control.c]
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2023-09-30 corrected errors and added instant stopping while moving through webserver
    [REST.c, Sailwind_Firmware.ioc, http_ssi_cgi.c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]
2023-09-30 added error setting and getting in REST
    [Linear_Guide.c, REST.c]
2023-10-01 added function for setting a max speed and a max allowed distance error
    [Linear_Guide.c, Motor.c, http_ssi_cgi.c]
2023-10-02 added functions to queue new desired positions, if they're not on the current way
2023-10-02 Localization is now saved on each position change and on resetting the center position
    [Linear_Guide.c, Manual_Control.c]
2023-10-02 changed switch operating mode function to toggle mode on each button edge
2023-10-02 REST: simplified sail adjustment json to +/- percentage (pitch / roll)
2023-10-04 added timer interrupt for moving buttons longpress to reset ip
    [Manual_Control.c, Sailwind_Firmware.ioc, main.c]
2023-10-04 fixed set center from cgi handler
    [LED.c, Linear_Guide.c, Manual_Control.c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]
2023-10-04 replaced all occurrences of trim with pitch
    [Linear_Guide.c, REST.c, Sailwind_Firmware.ioc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]
2023-10-05 stop motor when pressing both move buttons at the same time
2023-10-06 added blink timer interrupt and implemented setting / resetting of of ip address
    [FRAM.c, LED.c, Linear_Guide.c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]
2023-10-14 added switching between dhcp and static IP at runtime
2023-10-14 fixed webserver display off pitch roll percentage
    [http_ssi_cgi.c]
2023-10-14 added fixes for dhcp reset
    [Manual_Control.c, http_ssi_cgi.c]
2023-10-16 fixed saving of Localization data -> motor moves again
    [Linear_Guide.c, Test.c]
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2024-02-13 Added picture of Button and LED Layout and added usage desritpion
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2024-02-16 added Software/Motor sub chapter
    [SpeedRamp.xlsx]
2024-02-16 added Software/Steuerung der Linearführung/Kalibrierung Sub sub chapter and further headings
2024-02-17 added Software->Steuerung der Linearführung->Umsetzung einer Rollung/Trimmung sub sub chapter
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2024-02-20 added REST chapter and page brakes before all main sections

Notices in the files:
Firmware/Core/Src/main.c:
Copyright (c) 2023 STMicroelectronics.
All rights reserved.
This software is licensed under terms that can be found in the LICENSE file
